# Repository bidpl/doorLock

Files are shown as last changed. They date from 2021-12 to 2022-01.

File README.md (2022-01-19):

# Dorm Fingerprint Door Lock

A fingerprint activated doorlock that maintains key functionality (basically unlock door with finger but key still works if power goes out).

Prototyped with Shiv G. in Fall 2021 ECE 120 Honors lab.

## Control Board

v1.0
Apparently fingerprint sensor doesn't like 5V, it needs 3.3V. I read the documentation for the wrong sensor. Need 3.3V reg and decoupling caps for motor.

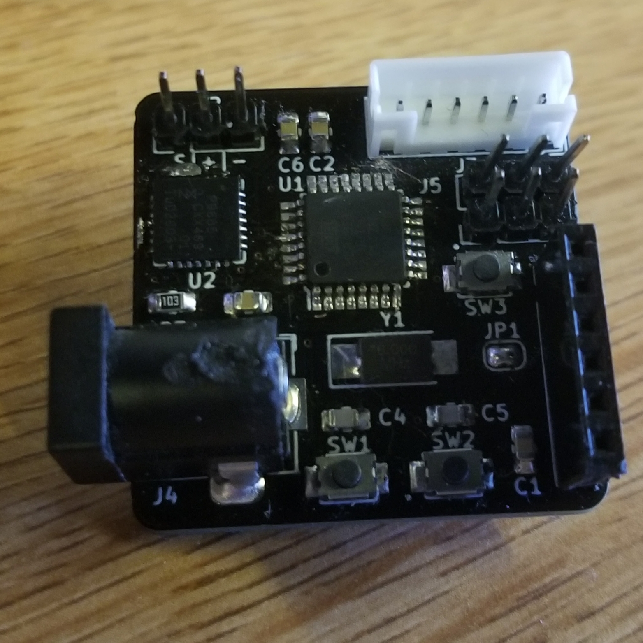
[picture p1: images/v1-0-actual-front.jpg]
Control Board v1.0 front view


v1.1
Added the 3.3V regulator, decoupling caps, seperated logic power from servo power with diode. Added test points and pin 13 led to help with debugging.

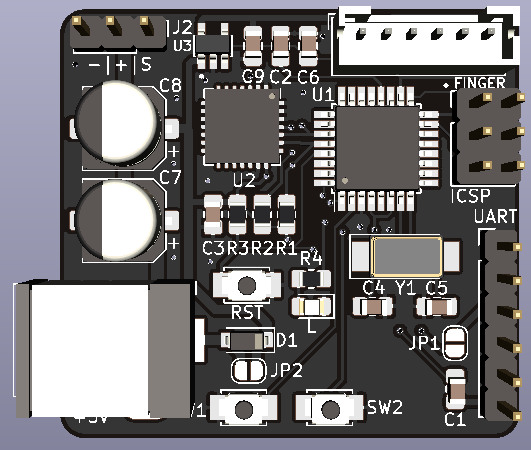
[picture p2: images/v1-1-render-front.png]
Control Board v1.1 render front view

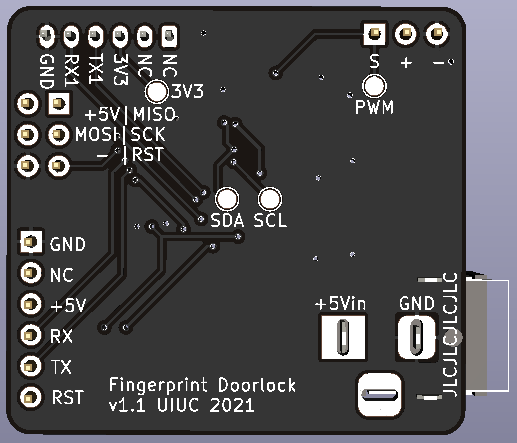
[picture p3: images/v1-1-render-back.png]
Control Board v1.1 render back view


## Mounting and Unlock Mechanism

Used a gear with an hourglass cutout to drive the lock spindle. The hourglass cutout gives the spindle enough space to lock and unlock using the key without hitting the gear. However, if driven past the clearance, the gear will still rotate the spindle.

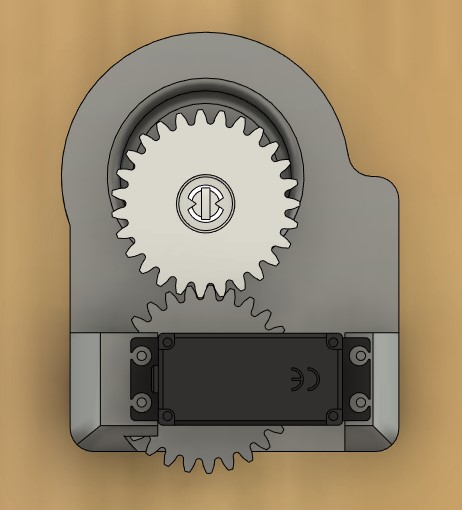
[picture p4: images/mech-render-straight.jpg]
Unlock Mechanism full render

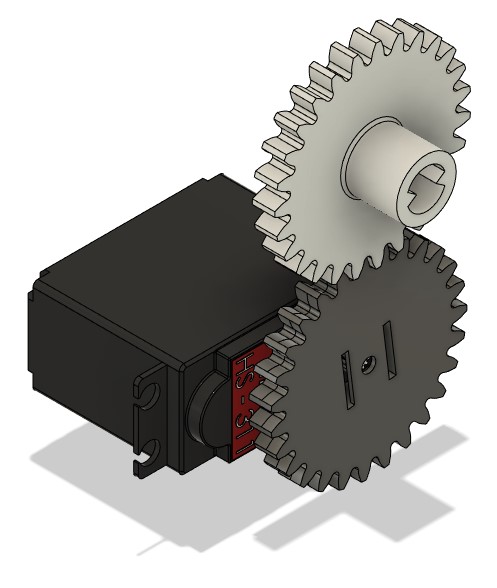
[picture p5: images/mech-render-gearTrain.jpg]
Unlock Mechanism geartrain


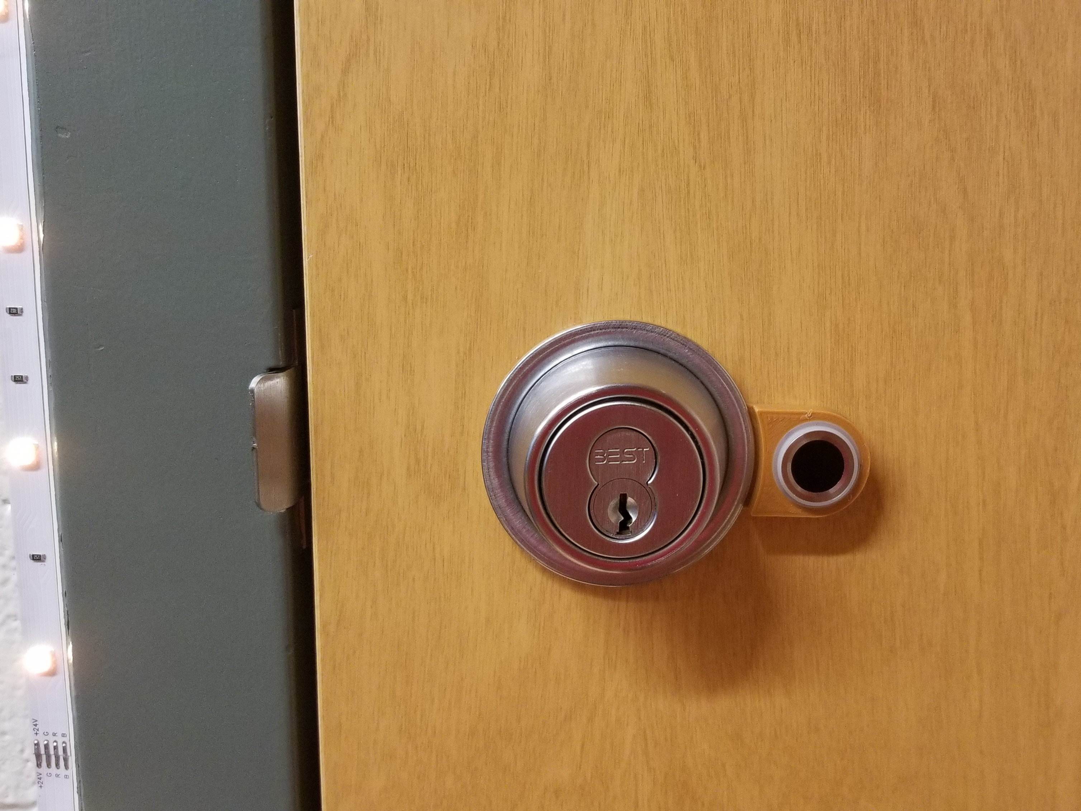
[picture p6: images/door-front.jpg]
Door front view

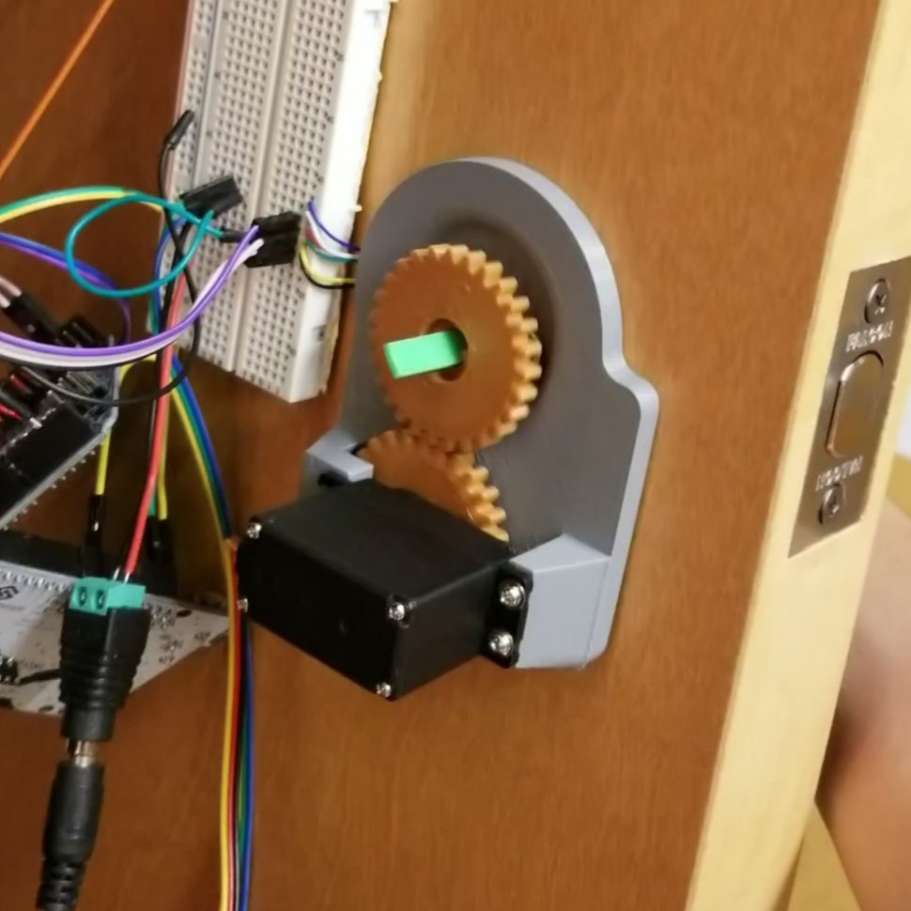
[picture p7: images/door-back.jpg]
Door back view


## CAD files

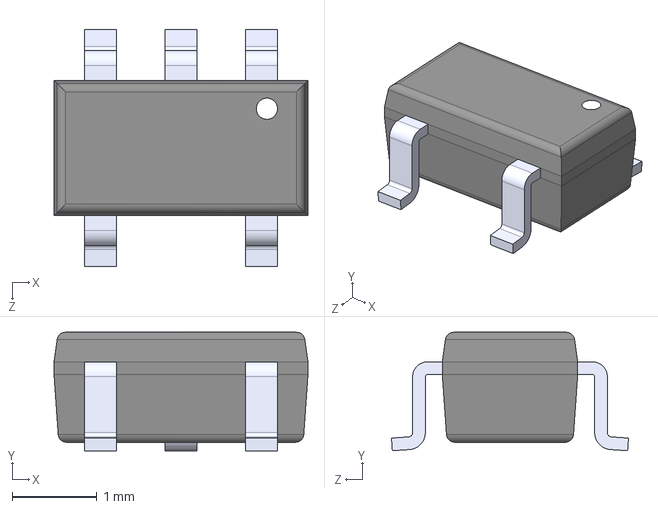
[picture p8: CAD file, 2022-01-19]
controlBoard/AP2112K-3.3TRG1/AP2112K-3.3TRG1.step
3.00 x 1.40 x 2.80 mm

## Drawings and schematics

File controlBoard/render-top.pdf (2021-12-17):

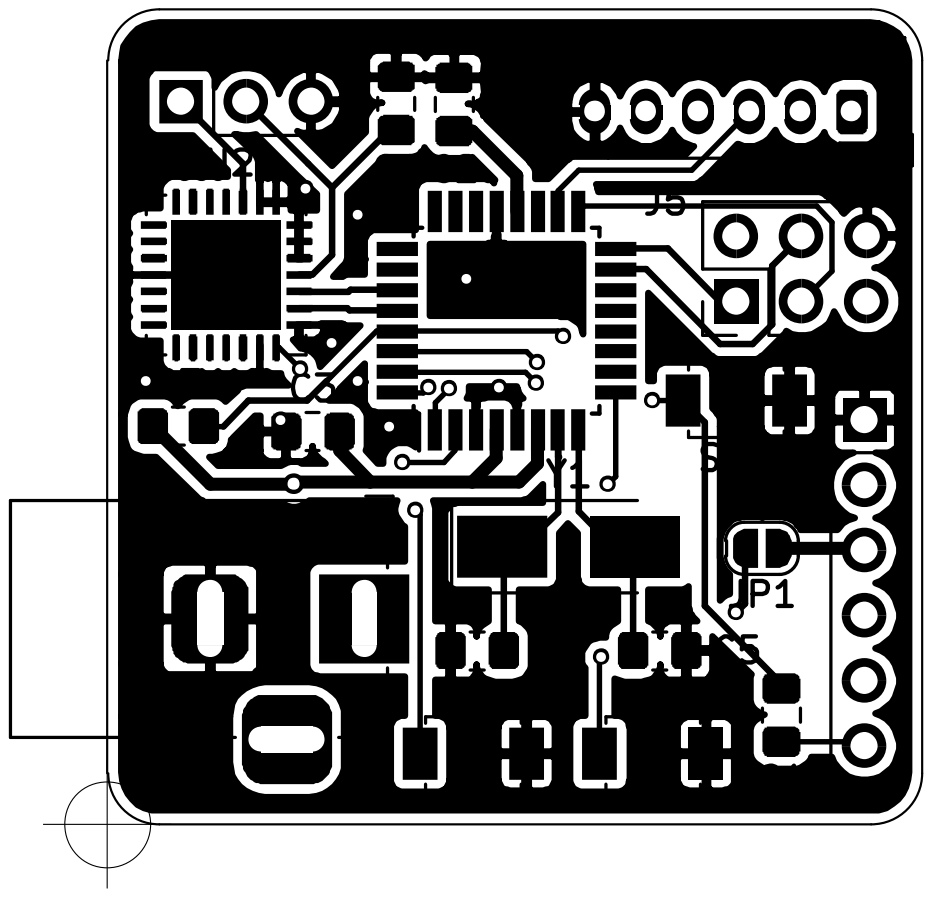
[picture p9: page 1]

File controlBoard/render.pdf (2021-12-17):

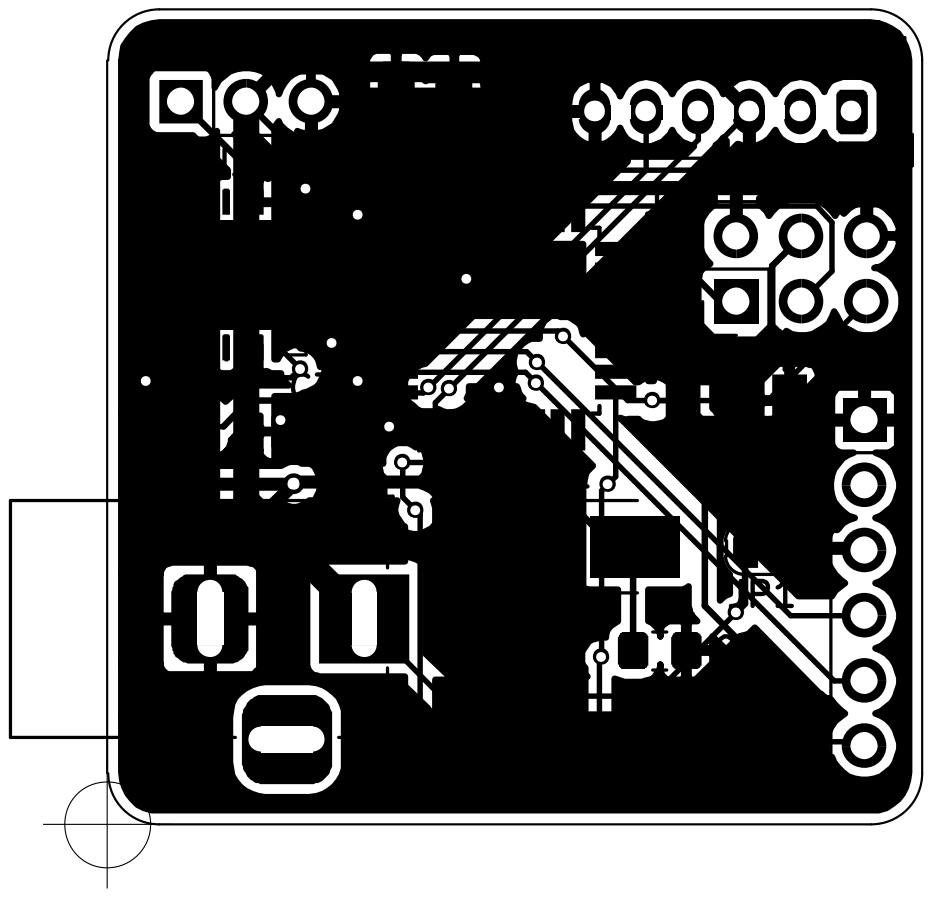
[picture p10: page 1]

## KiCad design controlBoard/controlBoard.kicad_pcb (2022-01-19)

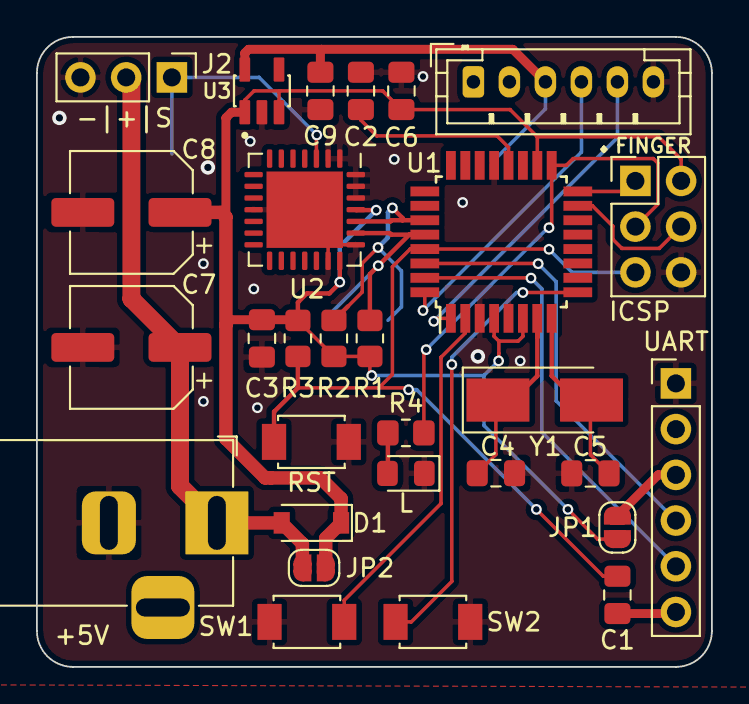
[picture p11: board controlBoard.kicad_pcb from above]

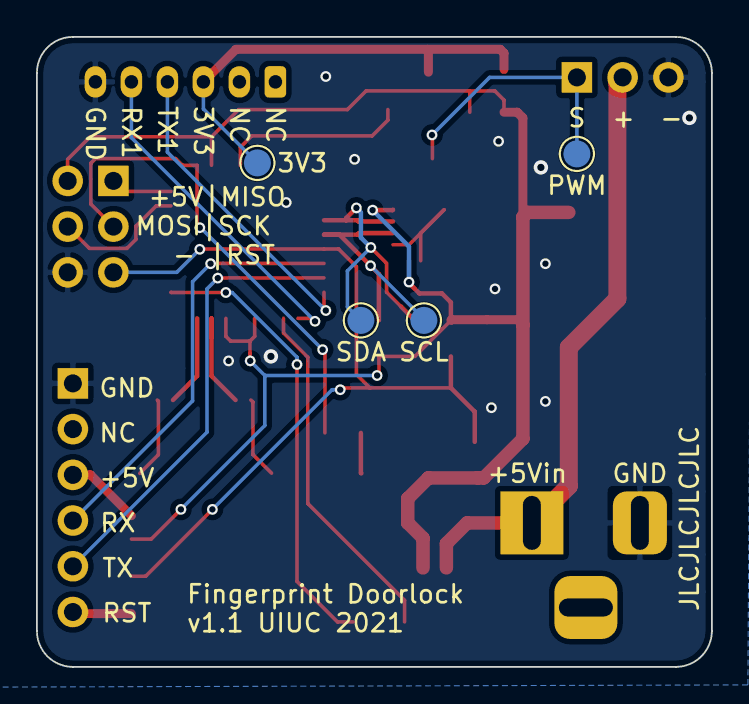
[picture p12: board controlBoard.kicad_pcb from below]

Board: 2 copper layers, 37.5 x 35.0 mm, 33 parts (4 on the bottom side), 23 nets.

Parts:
3V3: 3V3; TestPoint_Pad_D1.5mm
+5V: Barrel_Jack_Switch; BarrelJack_Horizontal
C1, C2, C3, C6, C9: 100n; C_0805_2012Metric_Pad1.18x1.45mm_HandSolder
C4, C5: 22p; C_0805_2012Metric_Pad1.18x1.45mm_HandSolder
C7, C8: 47u; CP_Elec_6.3x7.7
D1: D_Schottky; D_SOD-123
FINGER: Fingerprint; JST_PH_B6B-PH-K_1x06_P2.00mm_Vertical
ICSP: ICSP; PinHeader_2x03_P2.54mm_Vertical
J2: Servo; PinHeader_1x03_P2.54mm_Vertical
JP1, JP2: JVCC; SolderJumper-2_P1.3mm_Open_RoundedPad1.0x1.5mm
L: LED; LED_0805_2012Metric_Pad1.15x1.40mm_HandSolder
PWM: PWM; TestPoint_Pad_D1.5mm
R1, R2: 4k7; R_0805_2012Metric_Pad1.20x1.40mm_HandSolder
R3: 10k; R_0805_2012Metric_Pad1.20x1.40mm_HandSolder
R4: 1k; R_0805_2012Metric_Pad1.20x1.40mm_HandSolder
RST: SW_Push; SMD_Pushbutton_3mmx4mm
SCL: SCL; TestPoint_Pad_D1.5mm
SDA: SDA; TestPoint_Pad_D1.5mm
SW1, SW2: SW_Push; SMD_Pushbutton_3mmx4mm
U1: ATmega328P-AU; TQFP-32_7x7mm_P0.8mm
U2: PCA9685BS; QFN-28-1EP_6x6mm_P0.65mm_EP4.25x4.25mm
U3: AP2112K-3.3TRG1; SOT95P285X140-5N
UART: FTDI; PinHeader_1x06_P2.54mm_Vertical
Y1: Crystal; Crystal_SMD_5032-2Pin_5.0x3.2mm_HandSoldering

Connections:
+3V3: 3V3.1, C9.1, FINGER.3, U3.5
+5V: C3.2, C6.2, C8.1, D1.1, ICSP.2, JP1.2, JP2.2, R1.1, R2.1, R3.1, U1.4, U1.6, U1.18, U2.21, U2.25, U3.1, U3.3
+5VA: +5V.1, C7.1, D1.2, J2.2, JP2.1
/MISO: ICSP.1, U1.16
/MOSI: ICSP.4, U1.15
/PWM0: J2.1, PWM.1, U2.3
/Q: SW1.2, U1.2
/Q': SW2.2, U1.9
/RESET: C1.1, ICSP.5, R3.2, RST.1, U1.29
/RX: U1.30, UART.4
/RX1: FINGER.5, U1.1
/SCK: ICSP.3, R4.2, U1.17
/SCL: R1.2, SCL.1, U1.28, U2.23
/SDA: R2.2, SDA.1, U1.27, U2.24
/TX: U1.31, UART.5
/TX1: FINGER.4, U1.32
/XTAL+: C4.1, U1.7, Y1.1
/XTAL-: C5.1, U1.8, Y1.2
GND: +5V.2, C2.2, C3.1, C4.2, C5.2, C6.1, C7.2, C8.2, C9.2, FINGER.6, ICSP.6, J2.3, L.1, RST.2, SW1.1, SW2.1, U1.3, U1.5, U1.21, U2.1, U2.2, U2.11, U2.20, U2.22, U2.26, U2.27, U2.28, U2.29, U3.2, UART.1
unnamed: C1.2, UART.6
unnamed: C2.1, U1.20
unnamed: L.2, R4.1
unnamed: JP1.1, UART.3

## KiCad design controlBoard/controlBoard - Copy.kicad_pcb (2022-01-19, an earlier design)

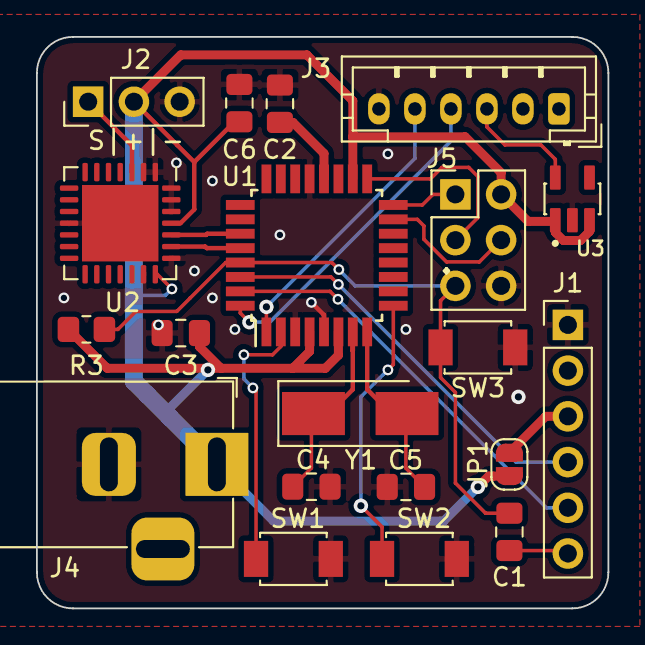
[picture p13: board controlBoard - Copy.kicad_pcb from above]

Board: 2 copper layers, 31.8 x 31.8 mm, 20 parts (0 on the bottom side), 21 nets.

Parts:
C1, C2, C3, C6: 100n; C_0805_2012Metric_Pad1.18x1.45mm_HandSolder
C4, C5: 22p; C_0805_2012Metric_Pad1.18x1.45mm_HandSolder
J1: FTDI; PinHeader_1x06_P2.54mm_Vertical
J2: Servo; PinHeader_1x03_P2.54mm_Vertical
J3: Fingerprint; JST_PH_B6B-PH-K_1x06_P2.00mm_Vertical
J4: Barrel_Jack_Switch; BarrelJack_Horizontal
J5: ICSP; PinHeader_2x03_P2.54mm_Vertical
JP1: JVCC; SolderJumper-2_P1.3mm_Open_RoundedPad1.0x1.5mm
R3: 10k; R_0805_2012Metric_Pad1.20x1.40mm_HandSolder
SW1, SW2, SW3: SW_Push; SMD_Pushbutton_3mmx4mm
U1: ATmega328P-AU; TQFP-32_7x7mm_P0.8mm
U2: PCA9685BS; QFN-28-1EP_6x6mm_P0.65mm_EP4.25x4.25mm
U3: AP2112K-3.3TRG1; SOT95P285X140-5N
Y1: Crystal; Crystal_SMD_5032-2Pin_5.0x3.2mm_HandSoldering

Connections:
+5V: C3.2, C6.2, J2.2, J4.1, J5.2, JP1.2, R3.1, U1.4, U1.6, U1.18, U2.21, U2.25, U3.1, U3.3
/MISO: J5.1, U1.16
/MOSI: J5.4, U1.15
/PWM0: J2.1, U2.3
/Q: SW1.2, U1.2
/Q': SW2.2, U1.9
/RESET: C1.1, J5.5, R3.2, SW3.1, U1.29
/RX: J1.4, U1.30
/RX1: J3.5, U1.1
/SCK: J5.3, U1.17
/SCL: U1.28, U2.23
/SDA: U1.27, U2.24
/TX: J1.5, U1.31
/TX1: J3.4, U1.32
/XTAL+: C4.1, U1.7, Y1.1
/XTAL-: C5.1, U1.8, Y1.2
GND: C2.2, C3.1, C4.2, C5.2, C6.1, J1.1, J2.3, J3.6, J4.2, J5.6, SW1.1, SW2.1, SW3.2, U1.3, U1.5, U1.21, U2.1, U2.2, U2.11, U2.20, U2.22, U2.26, U2.27, U2.28, U2.29, U3.2
unnamed: C1.2, J1.6
unnamed: C2.1, U1.20
unnamed: J1.3, JP1.1
unnamed: J3.3, U3.5

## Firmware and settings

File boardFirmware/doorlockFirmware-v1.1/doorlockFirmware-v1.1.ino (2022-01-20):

#include <Wire.h>
#include <DFRobot_ID809.h>
#include <SoftwareSerial.h>

SoftwareSerial mySerial(2, 3);
DFRobot_ID809 fingerprint;

byte value = 0;

byte fingerID = 0;

const int unlockID[] = {1,6};
const int lockID[] = {2,7};

const int unlockIDlen = sizeof(unlockID)/sizeof(unlockID[0]);
const int lockIDlen = sizeof(lockID)/sizeof(lockID[0]);


int actionID = 0;

void setup() {
  // Init serial port  
  Serial.begin(9600);
  Serial.setTimeout(10);
  Wire.begin();

  // set the data rate for the sensor serial port
  mySerial.begin(115200);

  //Link fingerprint to its serial port
  fingerprint.begin(mySerial);

  // Wait for serial port
  while(!Serial);

  while(!fingerprint.isConnected()){
    Serial.println("Communication with device failed, please check connection");
    /*Get error code information*/
    //desc = fingerprint.getErrorDescription();
    //Serial.println(desc);
    delay(1000);
  }
  
  //initialize pca9685
  //Enable sleep mode to change PRE_SCALE
  writeRegister(0x60, 0x00, 0x11);
  //Change PRE_SCALE to 7Dh (20ms period/50hz frequency)
  writeRegister(0x60, 0xFE, 0x7B);
  //Disable sleep mode/turn the internal osciallator on
  writeRegister(0x60, 0x00, 0x01);
}

void loop() {
  uint8_t fingerID = 0;
  /*Set fingerprint LED ring mode, color, and number of blinks
    Can be set as follows:
    Parameter 1:<LEDMode>
    eBreathing   eFastBlink   eKeepsOn    eNormalClose
    eFadeIn      eFadeOut     eSlowBlink   
    Parameter 2:<LEDColor>
    eLEDGreen  eLEDRed      eLEDYellow   eLEDBlue
    eLEDCyan   eLEDMagenta  eLEDWhite
    Parameter 3:<number of blinks> 0 represents blinking all the time
    This parameter will only be valid in mode eBreathing, eFastBlink, eSlowBlink
   */
  fingerprint.ctrlLED(/*LEDMode = */fingerprint.eBreathing, /*LEDColor = */fingerprint.eLEDBlue, /*blinkCount = */0);
  Serial.println("Please press down your finger");
  /*Capture fingerprint image, Disable the collection timeout function 
    If succeed return 0, otherwise return ERR_ID809
   */
  if((fingerprint.collectionFingerprint(/*timeout=*/0)) != ERR_ID809){
    /*Set fingerprint LED ring to quick blink in yellow 3 times*/
    fingerprint.ctrlLED(/*LEDMode = */fingerprint.eFastBlink, /*LEDColor = */fingerprint.eLEDYellow, /*blinkCount = */3);
    Serial.println("Capturing succeeds");
      Serial.println("Please release your finger");
    /*Wait for finger to release
      Return 1 when finger is detected, otherwise return 0 
     */
    while(fingerprint.detectFinger());
    
    /*Compare the captured fingerprint with all the fingerprints in the fingerprint library 
      Return fingerprint ID(1-80) if succeed, return 0 when failed 
     */
    fingerID = fingerprint.search();
    /*Compare the captured fingerprint with a fingerprint of specific ID 
      Return fingerprint ID(1-80) if succeed, return 0 when failed 
     */
    //fingerID = fingerprint.verify(/*Fingerprint ID = */1);  
    if(fingerID != 0){
      /*Set fingerprint LED ring to always ON in green */
      fingerprint.ctrlLED(/*LEDMode = */fingerprint.eKeepsOn, /*LEDColor = */fingerprint.eLEDGreen, /*blinkCount = */0);
      Serial.print("Matching succeeds,ID=");
      Serial.println(fingerID);
    }else{
      /*Set fingerprint LED ring to always ON in red*/
      fingerprint.ctrlLED(/*LEDMode = */fingerprint.eKeepsOn, /*LEDColor = */fingerprint.eLEDRed, /*blinkCount = */0);
      Serial.println("Matching fails");
    }
  }else{
    Serial.println("Capturing fails");
    /*Get error code information*/
    String desc = fingerprint.getErrorDescription();
    Serial.println(desc);
  }

  Serial.print("FingerID: ");
  Serial.println(fingerID);

  //Generate action based on fingerID
  //Defualt do nothing
  actionID = 0;

  for(int i = 0; i < unlockIDlen; i++){
    if(fingerID == unlockID[i]){
      actionID = 1;
      Serial.print("i: ");
      Serial.print(i);
      Serial.print("   unlockID[i]: ");
      Serial.print(unlockID[i]);
      Serial.println(fingerID == unlockID[i]);
    }
  }

  for(int i = 0; i < lockIDlen; i++){
    if(fingerID == lockID[i]){
      actionID = 2;
    }
  }

  //Fingerprint control
  if(actionID == 1){
    Serial.println("Unlocking");
    servoPulsePos(95);
  }
  
  if(actionID == 2){
    Serial.println("Locking");
    servoPulsePos(-95);
  }
  Serial.println("--------------");
}

byte readRegister(byte devAddr, byte regAddr){  
  Wire.beginTransmission(devAddr);
  Wire.write(regAddr);              // sends one byte
  Wire.endTransmission();    // stop transmitting


  Wire.requestFrom(devAddr, 1);
  byte data = Wire.read();
  return data;
}

byte writeRegister(byte devAddr, byte regAddr, byte data){
  Wire.beginTransmission(devAddr);
  Wire.write(regAddr);
  Wire.write(data);
  Wire.endTransmission();
}

void printRegister(byte devAddr, byte regAddr){
  Serial.print(devAddr, HEX);
  Serial.print(" ");
  Serial.print(regAddr, HEX);
  Serial.print(": ");
  Serial.println(readRegister(devAddr, regAddr), HEX);
}

void setPower(byte channel, int percentOutput){
  int output = 0x133 + 0x67 * percentOutput/100;
  
  //Set on time to 0
  writeRegister(0x60, 0x06 + 4*channel, 0);
  writeRegister(0x60, 0x07 + 4*channel, 0);
  //Set off time to 133h (307d) 1.5 ms pulse width
  writeRegister(0x60, 0x08 + 4*channel, output & 0xff);
  writeRegister(0x60, 0x09 + 4*channel, (output >> 8) & 0xff);

//  Serial.println(output & 0xff, HEX);
//  Serial.println((output >> 8) & 0xff, HEX);
}

void servoPulsePos(int pos){
  Serial.print("Servo to Position: "); Serial.println(pos);

  setPower(0, pos);

  delay(1000);

  setPower(0, 0);

  Serial.println("Return");
}

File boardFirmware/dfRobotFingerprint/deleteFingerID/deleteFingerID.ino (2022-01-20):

#include <DFRobot_ID809.h>
#include <SoftwareSerial.h>

SoftwareSerial Serial1(2, 3);  //RX, TX
#define FPSerial Serial1

DFRobot_ID809 fingerprint;


void setup() {
  // put your setup code here, to run once:
  /*Init print serial port*/
  Serial.begin(9600);
  /*Init FPSerial*/
  FPSerial.begin(115200);
  /*Take FPSerial as communication serial port of the fingerprint module */
  fingerprint.begin(FPSerial);
  /*Wait for Serial to open*/
  while(!Serial);
  /*Test whether the device can properly communicate with mainboard
    Return true or false
    */
  while(fingerprint.isConnected() == false){
    Serial.println("Communication with device failed, please check connection");
    /*Get error code information*/
    //desc = fingerprint.getErrorDescription();
    //Serial.println(desc);
    delay(1000);
  }

  Serial.println("EnterID to delete: ");
}

void loop() {
  // put your main code here, to run repeatedly:
  if(Serial.available()) {
    int id = Serial.parseInt();

    fingerprint.delFingerprint(id);

    Serial.print("Deleted id " );
    Serial.println(id);
  }
}

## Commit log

2021-12-10 Tested arduino to arduino i2c communication
2021-12-15 Fixed test serialToI2C.ino and added kicad files
    [controlBoard.kicad_pcb, controlBoard.sch]
2021-12-17 Added button footprint and layout pcb
    [controlBoard.kicad_pcb, controlBoard.sch]
2021-12-21 Swapped TX1 and RX1 pins, cleaned up board a bit to send off to production
    [controlBoard-B_Cu.gbl, controlBoard-B_Mask.gbs, controlBoard-B_Paste.gbp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]
2022-01-01 Added 2 electrolytic caps, pin 13 led, 3v3 linear reg, seperated power for logic and servo, increased board size, rotated some headers, added some test points
    [AP2112K-3.3TRG1.step, controlBoard - Copy.kicad_pcb, controlBoard.kicad_pcb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]
2022-01-12 Added decoupling cap for fingerprint reader, generated gerbers
    [controlBoard-B_Cu.gbl, controlBoard-B_Mask.gbs, controlBoard-B_Paste.gbp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]
2022-01-18 Added 3d footprints to pcb, edited README.md
    [controlBoard.kicad_pcb]
2022-01-20 Ported boardfirmware to new fingerprint sensor (doorlockFirmware-v1.1), only tested on breadboard
